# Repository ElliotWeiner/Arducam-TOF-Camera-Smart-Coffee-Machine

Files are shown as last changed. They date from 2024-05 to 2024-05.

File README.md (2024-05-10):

# Arducam TOF Camera Smart Coffee Machine

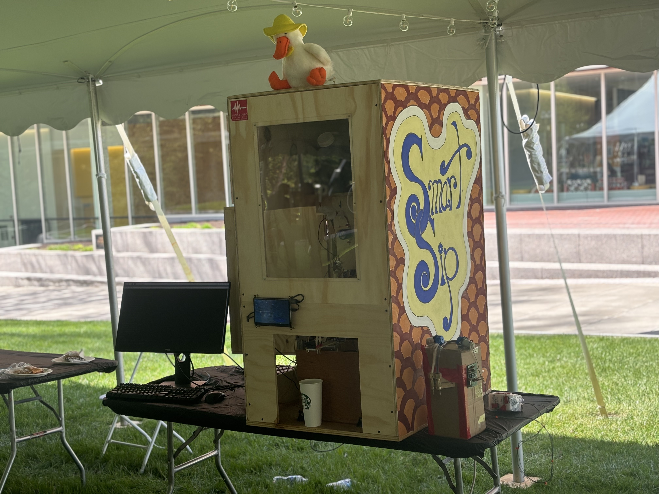
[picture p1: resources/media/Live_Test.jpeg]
Picture of Experimental Design

 
*Experimental Design*

## Project Summary

This repository contains the source code for an autonomous coffee dispenser, informally named 'SmartSip'. Its intended use is to reduce the workload of baristas by acting as an 'extra hand' that can pour simple drinks with little assistance from a user. Due to its improvements on previous pouring technologies, it could easily be adapted for a broader scope of commercial implementations. 
 
The machine hosts unique features that make it ideal for high-customer volume environments: automated cup centering under a custom-built nozzle, cup volume estimation, and hands-free drink pouring based on user input proportioning. These expand upon mainstream liquid dispensing methods, in which drinks are proportioned with a static volume or only one liquid is poured (commonly seen in auto-fill implementations). SmartSip accomplishes these tasks by using [Arducam’s Time of Flight Camera (TOF) for Raspberry Pi](https://www.arducam.com/time-of-flight-camera-raspberry-pi/), which allows the machine to detect changes in range with a surprising degree of accuracy.

## Hardware

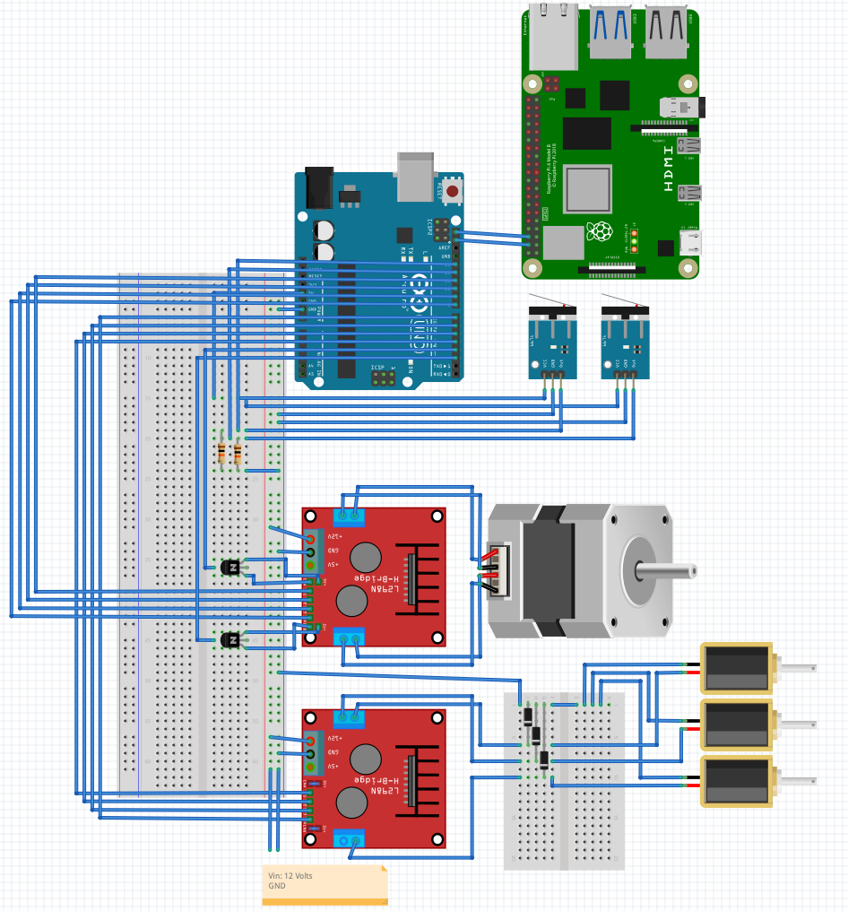
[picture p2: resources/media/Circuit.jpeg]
Circuit Layout


*Full Circuit Diagram*

#### Microcontrollers
A Raspberry Pi 4 was used as the 'main' node, taking in user input and serving as the central hub of decision-making and communications. It used the Ubuntu 20.04 operating system to allow for ROS compatibility in future applications. However, this presented issues when implemented alongside the Arducam TOF Camera, as it was designed with only Raspbian compatibility in mind. For this reason, a Raspberry Pi 3 was configured with the Raspbian OS and TCP communication capabilities, allowing for seamless data transfer between the two. Additionally, an Arduino Uno was selected as a hardware controller due to its compatibility with physical components (such as limit switches, stepper motors, etc).

#### One Stepper Motor
Gantry Test 

*Gantry System Testing*
 
A stepper motor was used to control the gantry system, which is shown above. Because of its high precision, it provided the system with an accurate method for positioning the attached nozzle.
 
#### Two Limit Switches
Limit switches were used in combination with the stepper motor to simplify gantry control. By attaching them to the ends of the track, the motor could be stopped automatically by the controller, which led to additional ‘self-reset’ capabilities.
 
#### Three Solenoid Valves
In order to implement a simple fluid control system, solenoids were attached at the halfway point between filled ingredient tanks and the nozzle. These allowed for reliable control of pouring systems, making them ideal for a proof of concept (POC) prototype. The main downside of these valves was the lack of static flow rate. Because the fluid system was gravity-powered, the flow rates were entirely reliant upon the tanks’ fullness.

## Arducam TOF Camera

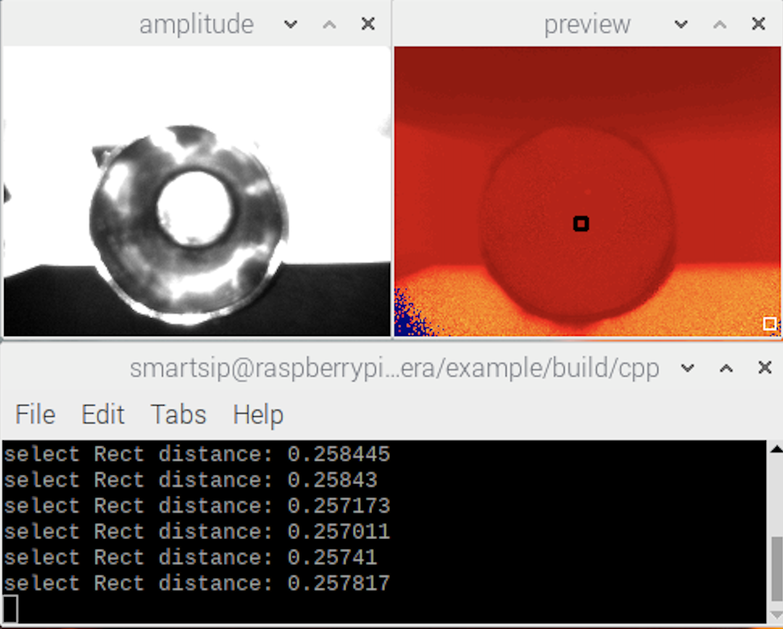
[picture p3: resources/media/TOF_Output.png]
TOF Output


*Example Camera Preview*

The Arducam TOF Camera was used to provide inference capability to the machine. By generating depth images (and from that, laser scans), information about the ground height, the position of a given cup’s rims, and general cup measurements could be acquired and processed. The code for these functions can be found in the RPi3 folder under camera_node.py, which details our centering algorithms, bearing adjustments, volume calculations, and laser scan generation.

One of the main reasons we chose to use the TOF camera was due to its low price, making the project more affordable. However, we discovered that it had several drawbacks — the most notable of these being the inconsistency between laser scans. It was noticed early on in our testing that no two depth frames gave consistent measurements for range values at the same locations. Unfortunately, consistent millimeter precision was nearly impossible without an algorithmic solution, and there didn’t seem to be a consistent pattern to the differences. Because of this imprecision, we replaced the original method of volume estimation, which calculated volume by observing the liquid height and flow rate. In its place, we implemented a cylindrical calculation, which featured minor adjustments tailored to improve precision. Additionally, a substantial error was observed in detecting rim heights above 10 centimeters. This error was due to the proximity of the sensor to certain cup rims, in addition to the sensitivity of lidar technology. To solve this issue, we implemented an error-accommodation function $0.005 *(x-10)^{1.8}$ $while$ $x > 10$ where x was measured in meters, allowing for a repeatedly accurate estimation of volume.

## Communication Protocols

### TCP

Transmission Control Protocol (TCP) was used to instantiate basic communication between the Raspberry Pi 3 and 4. The python [‘Socket’ Library](https://www.geeksforgeeks.org/socket-programming-python/) made this relatively simple, which can be observed in the implementations for RPi3 and RPi4. The RPi3 code can be located in the camera_node.py file (client), while that for the RPi4 is found both in centering.py (server) and an interface configuration file named set_static_eth0. To work correctly, this file must be moved to the /etc/network/interfaces.d folder to allow for static eth0 initialization on bootup (note: this action will disable wireless connection on the device until it is removed).

### I2C

We implemented Inter-Integrated Circuit (I2C) communication to connect the RPi4 (master node) with the Arduino Uno hardware controller (slave node). Through this connection, commands could be sent regarding solenoid and stepper motor control. This setup was facilitated primarily through the use of the python [SMBus Library](https://pypi.org/project/smbus/) and the Arduino IDE [Wire.h Class](https://www.arduino.cc/reference/en/language/functions/communication/wire/)
Limit switch data was dealt with directly by the hardware controller. The code for this can be found in the RPi4 centering.py file and the Arduino Uno controller.ino file.

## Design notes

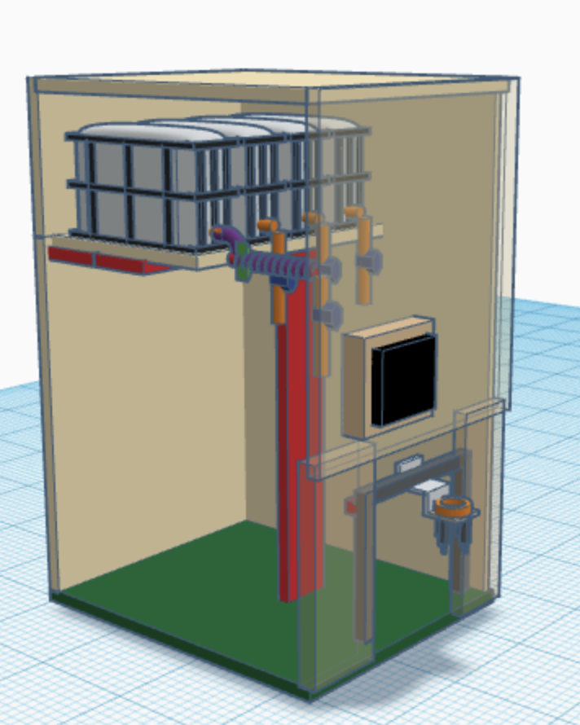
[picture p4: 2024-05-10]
resources/media/TinkerCAD_Preview.png

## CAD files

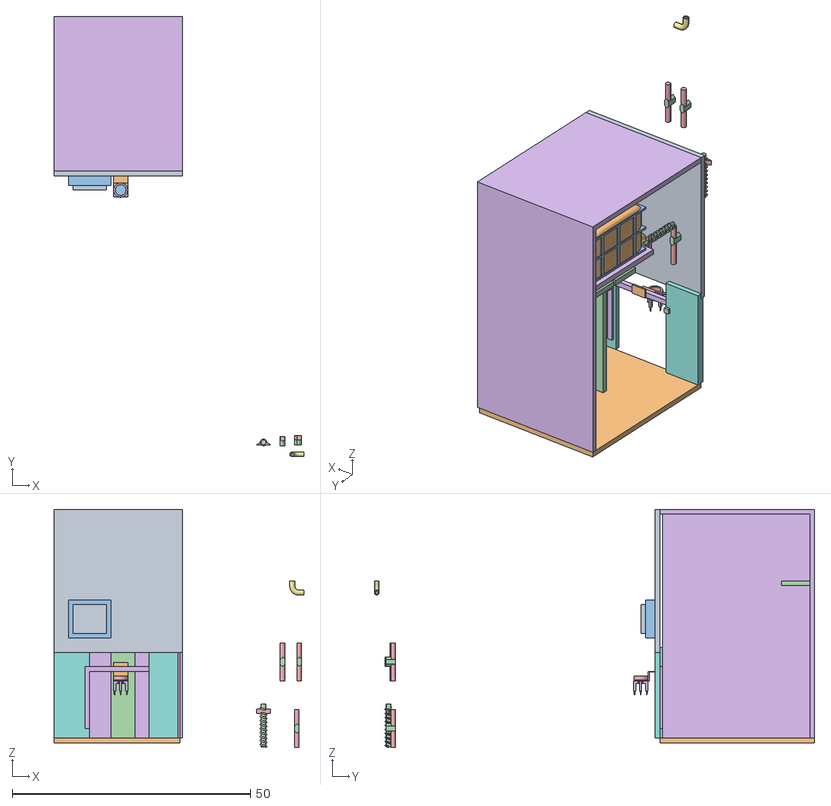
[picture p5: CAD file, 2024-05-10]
resources/schematics/smartSip/tinker.obj
52.5 x 92.5 x 50.0

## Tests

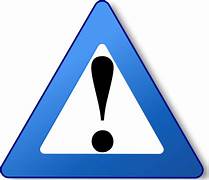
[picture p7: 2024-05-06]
RPi4/software/testing/TS/smartSip/warning.jpg

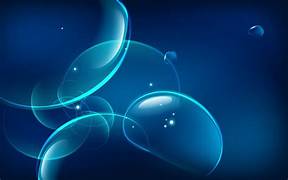
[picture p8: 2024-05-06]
RPi4/software/testing/TS/smartSip/bubbles.jpg

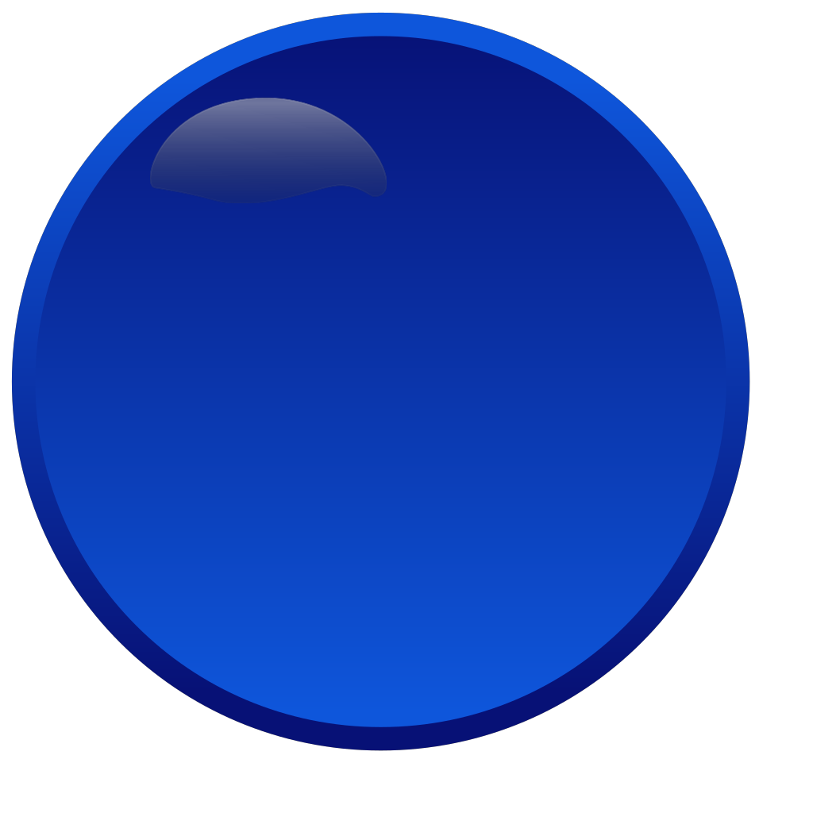
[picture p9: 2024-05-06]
RPi4/software/testing/TS/smartSip/rbutton.png

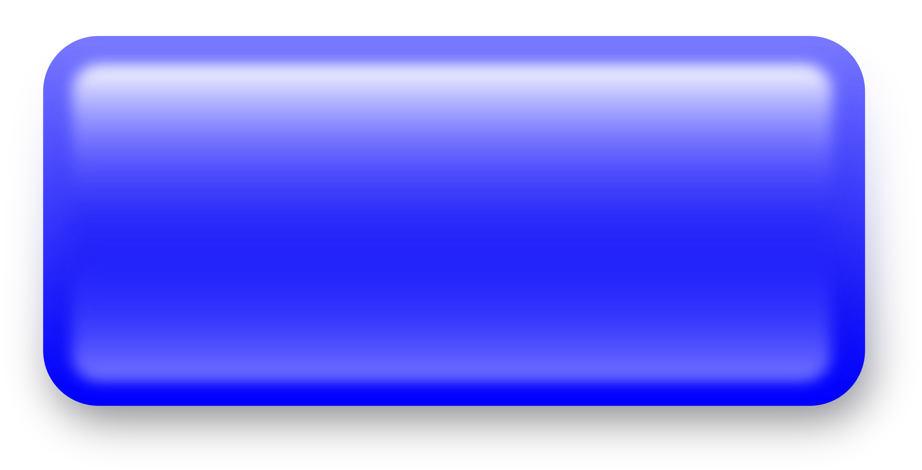
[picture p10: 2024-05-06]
RPi4/software/testing/TS/smartSip/widget.png

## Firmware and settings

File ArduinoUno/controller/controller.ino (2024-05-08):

// Author: Elliot Weiner
// Date: 04 / 03 / 2024
// Organization: University of Rochester Electrical and Computer Engineering Department
// Description:
//   This code allows the Arduino Uno to function as a hardware controller. It takes in commands from an I2C communication channel with
//   the Raspberry Pi 4 and translates them into actual motor control. Pinouts can be derived from the following set of pin initializations.
//

#include <Wire.h>
#include <Stepper.h>

// solenoid init
const int Sol1_Pin = 4;
const int Sol2_Pin = 5;
const int Sol3_Pin = 6;
const int Sol4_Pin = 7;

// enable pin init ( for gantry system )
const int en1 = 2;
const int en2 = 3;

// limit switch init
// left
const int lim_1 = 13;
int lim_1_val = 0;
// right
const int lim_2 = 12;
int lim_2_val = 0;

// last command
int last_command;


// init stepper motors ( for gantry system )
const int stepsPerRevolution = 200;
Stepper myStepper(stepsPerRevolution, 11, 10, 9, 8);
int direction = 0;


// setup
void setup() {
  // Join I2C bus as follower
  Wire.begin(0x8);
  Wire.onReceive(receiveEvent);

  // Limit switches
  pinMode(lim_1, INPUT);
  pinMode(lim_2, INPUT);

  // Setup Solenoid Pins
  pinMode(Sol1_Pin, OUTPUT);
  pinMode(Sol2_Pin, OUTPUT);
  pinMode(Sol3_Pin, OUTPUT);
  pinMode(Sol4_Pin, OUTPUT);

  // Setup enable pins for motor
  pinMode(en1, OUTPUT);
  pinMode(en2, OUTPUT);

  // set the speed at 50 rpm:
  myStepper.setSpeed(50);
  // initialize the serial port:
  Serial.begin(9600);


}

// set stepper motor speed
void setSpeed(int dir) {
  // stop solenoid pouring
  digitalWrite(Sol1_Pin, LOW);
  digitalWrite(Sol2_Pin, LOW);
  digitalWrite(Sol3_Pin, LOW);
  digitalWrite(Sol4_Pin, LOW);

  // set direction
  // enable and disable enable pins to regulate current flow to stepper motors
  if ( dir == 1 ) {
    direction = 100;
    digitalWrite(en1, HIGH);
    digitalWrite(en2, HIGH);
  }
  else if ( dir == 2 ) {
    direction = -100;
    digitalWrite(en1, HIGH);
    digitalWrite(en2, HIGH);
  }
  else {
    direction = 0;
    digitalWrite(en1, LOW);
    digitalWrite(en2, LOW);
  }
}

// set solenoid output
void setSol(int dir) {
  // disable stepper motor
  direction = 0;
  digitalWrite(en1, LOW);
  digitalWrite(en2, LOW);

  // clear solenoid pinout
  digitalWrite(Sol1_Pin, LOW);
  digitalWrite(Sol2_Pin, LOW);
  digitalWrite(Sol3_Pin, LOW);
  digitalWrite(Sol4_Pin, LOW);

  // Enable specific solenoid
  if ( dir == 3 ) {
    digitalWrite(Sol1_Pin, HIGH);
    Serial.println(dir);
  }
  else if ( dir == 4 ) {
    digitalWrite(Sol2_Pin, HIGH);
    Serial.println(dir);
  }
  else if ( dir == 5 ) {
    digitalWrite(Sol3_Pin, HIGH);
    Serial.println(dir);
  }
  else if ( dir == 6 ) {
    digitalWrite(Sol4_Pin, HIGH);
    Serial.println(dir);
  }
}


void loop() {
  // motor step
  myStepper.step(direction);

  //set limits 
  lim_1_val = digitalRead(lim_1);
  lim_2_val = digitalRead(lim_2);
  
  // hit right
  if( lim_2_val == 1 ) {
    Serial.println("Hit right!");
    setSpeed(0);
    Serial.println("move to restart");
    moveToStart();
    Serial.println("restarted");
  }

  // if moving left, hit left
  if( last_command == 1 ) {
    if( lim_1_val == 1 ) {
    Serial.println("Hit left!");
    setSpeed(0);
    Serial.println("restarted");
  }

  }
}

// move to start position
void moveToStart() {
  setSpeed(1);
  Serial.println("restarting");
  while( lim_1_val != 1 ) {
    lim_1_val = digitalRead(lim_1);
    myStepper.step(direction);
  }
  setSpeed(0);
}

// RPi4 I2C recieve event
void receiveEvent(int howMany) {
  while (Wire.available()) {
    // get message
    int in = Wire.read();
    Serial.println(in);

    last_command = in;

    // Speed
    if (in == 0 || in == 1 || in == 2) {
      setSpeed(in);
    }
    // Pour
    else if (in == 3 || in == 4 || in == 5 || in == 6 || in == 7){
      setSol(in);
    }
  }
}

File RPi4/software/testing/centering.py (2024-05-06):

# Author: Elliot Weiner
# Date: 04 / 03 / 2024
# Organization: University of Rochester Electrical and Computer Engineering Department
# Description:
#   This code serves as the backend control for the entirety of the coffee machine. It interpets camera_node.py's TCP-based messages and makes 
#   decisions on cup centering and pouring. These decisions are then sent via I2C to a hardware controller.
#


import socket
import smbus
import time

# initialize socket communication
def int_com(s):

    # socket setup
    host = '169.254.12.13'
    port = 9009
    s.bind(('', port))

    s.listen( 1 )

# center a given cup
def center(c, bus, address):
    # sync with camera_node.py
    print("connected to by :", addr)
    c.send(b'Ready to make some coffee?')
    
    time.sleep(0.1)

    # start search
    bus.write_byte( address , 2 )
    centered = False;

    while not centered:
        # wait until camera node sends found code 1
        inp = int(c.recv(1024).decode())
        print(inp)

        if inp == 1:
            bus.write_byte( address , 0 )
            print('centered!')
            centered = True

# pour based on volume estimate and given proportions
def pour(vol, bus1, address1, recipe):
    # experimentally calculated flowrates
    flowrates = [0.2, 0.2, 0.2]

    # for each ingredient in recipe, pour
    for i in range(len(recipe)):
        # pour time
        t = vol * recipe[i] / flowrates[i] # oz * % / oz * s = s
        
        string =" pouring ingredient " + str(i) + " for " + str(t) + " seconds."
        print(string)
        
        # pour
        bus1.write_byte(address1, 3+i)
        time.sleep(t)
        bus1.write_byte(address1, 7)

    return

# get a recipe from a txt file
def get_recipe():
    while(1):
        # get text file
        text = open('TS/smartSip/orders.txt', 'r')
        text = text.readlines()

        # convert txt contents to recipe array
        if len(text) > 0:
            recipe = [0.0,0.0,0.0]
            for line in text:
                split = line.split(':')
                
                if split[0] == "Milk":
                    recipe[1] = float(split[1]) / 100
                elif split[0] == "Coffee":
                    recipe[2] = float(split[1]) / 100
                elif split[0] == "Non-Dairy":
                    recipe[0] = float(split[1]) / 100
            return recipe

if __name__ == '__main__':

    # init socket communication
    sock = socket.socket()
    int_com(sock)

    # init bus specs
    address1 = 0x8
    bus1 = smbus.SMBus( 1 )

    # init com bus
    c, addr = sock.accept()

    while(1):
        # get recipe
        recipe = get_recipe()
        print(recipe)

        # center
        center(c, bus1, address1)

        # sync centering_node.py
        time.sleep(1)
        msg = "Pouring"
        c.send(msg.encode())

        
        
        # get volume estimate and pour
        vol = float(c.recv(1024).decode())
        pour(vol, bus1, address1, recipe)
        
        # clear file
        text = open('TS/smartSip/orders.txt', 'w')
        text.close()
        
        # reset nozzle position and break
        print("time to reset")
        bus1.write_byte(address1, 1)
        time.sleep(5)
        

    # close coms
    c.close()
    sock.close()

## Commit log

2024-05-10 Added schematic files
    [tinker.obj]
2024-05-11 Added circuit schematics
    [Circuit_Diagram.fzz]
